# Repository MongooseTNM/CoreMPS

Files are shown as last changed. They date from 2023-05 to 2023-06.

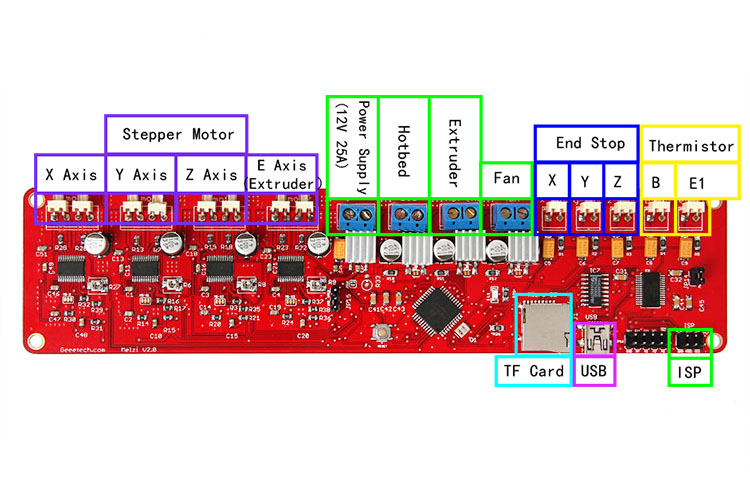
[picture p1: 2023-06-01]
Wiring Diagram.jpg

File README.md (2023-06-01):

# CoreMPS


The CoreMPS is a complete rebuild of the once-popular Monoprice Maker Select V2 3d printer. The CoreMPS replaces everything except the electronics, heater bed, and hot-end components. The frame was replaced with an aluminum extrusion cube design as opposed to the sheet metal the Monoprice Maker Select V2 came with. 

The CoreMPS also makes use of 3D-printed parts wherever possible in the spirit of RepRap. Reprap is a project started in 2010 that aims to allow printers to self-replicate, meaning that parts are designed and printed on the machine that the part was designed for. All the parts for the CoreMPS were designed with 3d printing in mind, there are no unprintable overhangs and the parts are strong enough to handle loads of high-speed printing. 

The CoreMPS uses CoreXY kinematics, meaning that 2 stationary motors move the gantry in both directions. When the motors rotate in the same direction the gantry will move left and right (X direction) and when the motors rotate in opposite directions then the gantry will move forward and backward (Y direction). If only one motor rotates the gantry will move at a 45-degree angle.

Building the CoreMPS requires pre-existing knowledge of building 3D printers and working with Raspberry Pis. The CoreMPS was designed from scratch over the course of a few weeks and built over the course of a week while parts arrived.

The CoreMPS is capable of printing at 300mm/s and 30k mm/s/s accelerations. Normal non-coreXY printers are usually capable of at most 100mm/s and 5k mm/s/s accelerations. This means that the CoreMPS can print objects up to 100% faster than normal non-coreXY printers.

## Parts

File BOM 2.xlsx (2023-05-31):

Item # | Thumbnail | Part Name | Part Number | Description | Make/Buy | Quantity | Vendor | Vendor Desc | Vendor P/N | Vendor URL | Vendor Price | Vendor Lot Size | Vendor Stock
 |  | MPS CoreXY | MPS CoreXY |  |  | 1
1 |  | HotBed | HotBed |  |  | 1
2 |  | 15mm Rev Extrusion 340mm Z | 15mm Rev Extrusion 340mm Z |  |  | 4
3 |  | 15mm Rev Extrusion 310mm X | 15mm Rev Extrusion 310mm X |  |  | 5
4 |  | 15mm Rev Extrusion 330mm Y | 15mm Rev Extrusion 330mm Y |  |  | 4
5 |  | MGN9H 300mm Y | MGN9H 300mm Y |  |  | 2
6 |  | Joint | Joint |  |  | 1
7 |  | MGN9H 250mm X | MGN9H 250mm X |  |  | 1
8 |  | Z Axis 8mm Linear Rod | Z Axis 8mm Linear Rod |  |  | 4
9 |  | Stepper Mount Z | Stepper Mount Z |  |  | 2
10 |  | Bottom Smooth Rod Mount Z | Bottom Smooth Rod Mount Z |  |  | 4
11 |  | Top Smooth Rod Mount Z | Top Smooth Rod Mount Z |  |  | 4
12 |  | Bed Mount | Bed Mount |  |  | 2
13 |  | Brass Nut | Brass Nut |  |  | 2
14 |  | LM8UU | LM8UU |  |  | 8
15 |  | i3_mk2 extruder | i3_mk2 extruder |  |  | 1
16 |  | Corner Brace | Corner Brace |  |  | 8
17 |  | F623ZZ Flange Bearing | F623ZZ Flange Bearing |  |  | 24
18 |  | Front Right Bearing Mount | Front Right Bearing Mount |  |  | 1
19 |  | Front Left Bearing Mount | Front Left Bearing Mount |  |  | 1
20 |  | Nema 17 34mm Lead Screw | Nema 17 34mm Lead Screw |  |  | 2
21 |  | Nema 17 48mm | Nema 17 48mm |  |  | 2
22 |  | GT2 20T5B_dz2020 | GT2 20T5B_dz2020 |  |  | 2
23 |  | Belts 4M needed | Belts 4M needed |  |  | 2
24 |  | Corner Gusset With Feet | Corner Gusset With Feet |  |  | 4
25 |  | Stepper Motor Mount Mirror | Stepper Motor Mount Mirror |  |  | 1
26 |  | Tall Bearing Spacer | Tall Bearing Spacer |  |  | 6
27 |  | Short Bearing Spacer | Short Bearing Spacer |  |  | 2
28 |  | Stepper Motor Bearing Brace | Stepper Motor Bearing Brace |  |  | 2
29 |  | Melzi Bracket | Melzi Bracket |  |  | 1
30 |  | Corner Gusset | Corner Gusset |  |  | 2
31 |  | Front Corner Gusset | Front Corner Gusset |  |  | 1
32 |  | melzi | melzi |  |  | 1
33 |  | Raspberry Pi Mount | Raspberry Pi Mount |  |  | 1
34 |  | Raspberry Pi 3B | Raspberry Pi 3B |  |  | 1
35 |  | Power Supply | Power Supply |  |  | 1
36 |  | Power Supply Mount | Power Supply Mount |  |  | 1
37 |  | Plug Mount | Plug Mount |  |  | 1
38 |  | Plug | Plug |  |  | 1
39 |  | Corner Bracket | Corner Bracket |  |  | 19

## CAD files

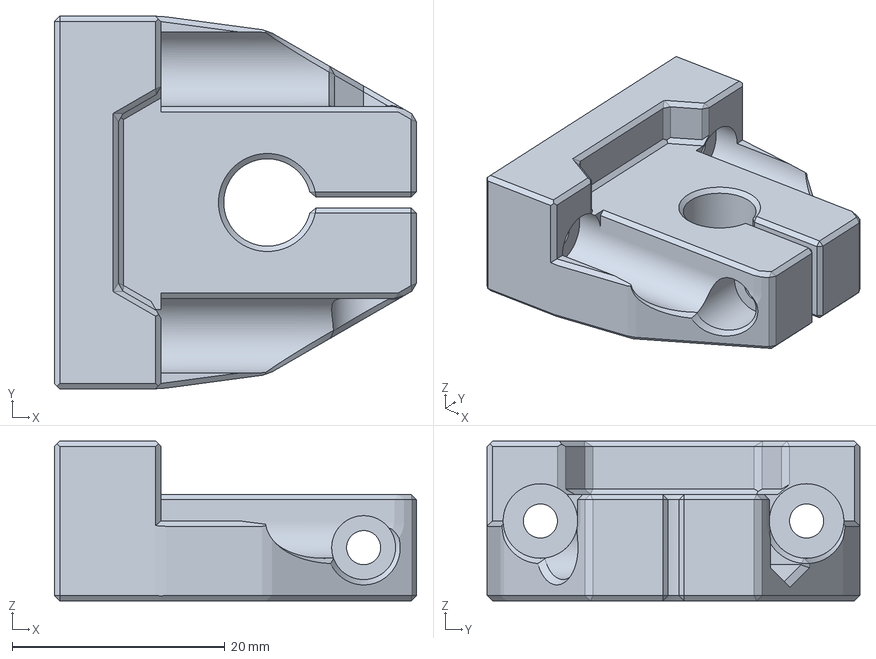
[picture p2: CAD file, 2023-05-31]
3D Printed Parts/4x Bottom Smooth Rod Mount Z v8.3mf
34.0 x 35.0 x 15.0 mm

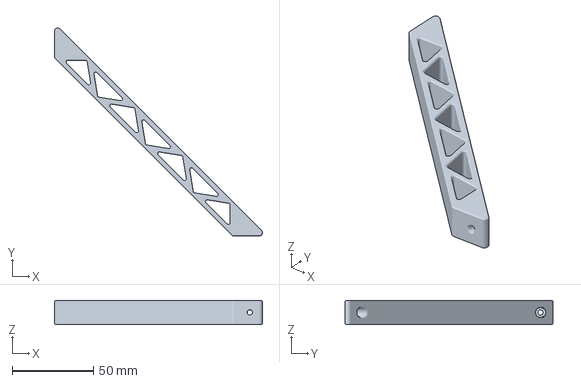
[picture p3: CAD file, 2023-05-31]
3D Printed Parts/8x Corner Brace v17.3mf
127.8 x 127.8 x 15.0 mm

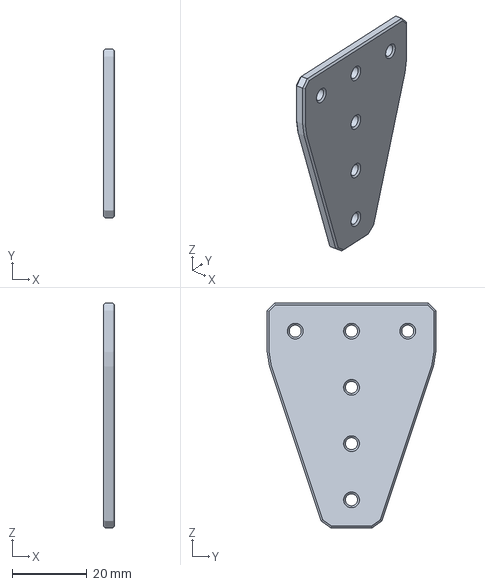
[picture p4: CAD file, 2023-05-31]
3D Printed Parts/3x 3 Way 180 Degree Corner Gusset v2.3mf
3.00 x 45.0 x 60.0 mm

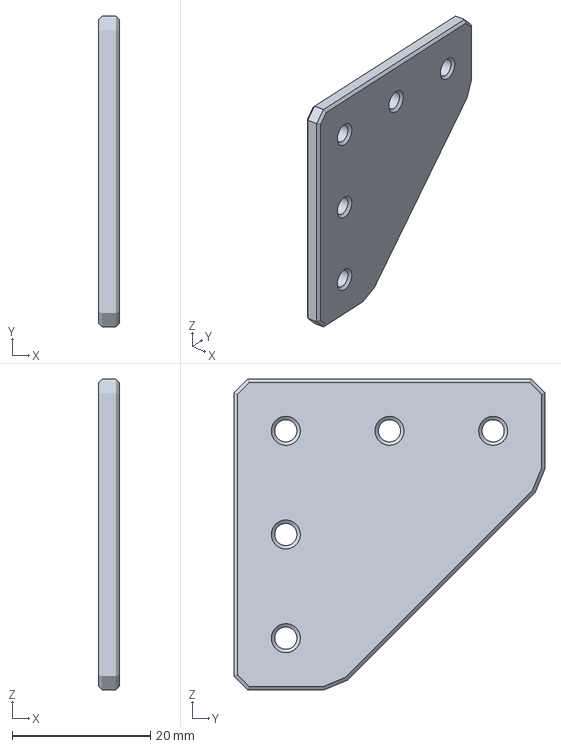
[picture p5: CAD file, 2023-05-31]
3D Printed Parts/2x 90 Degree Corner Gusset v2.3mf
3.00 x 45.0 x 45.0 mm

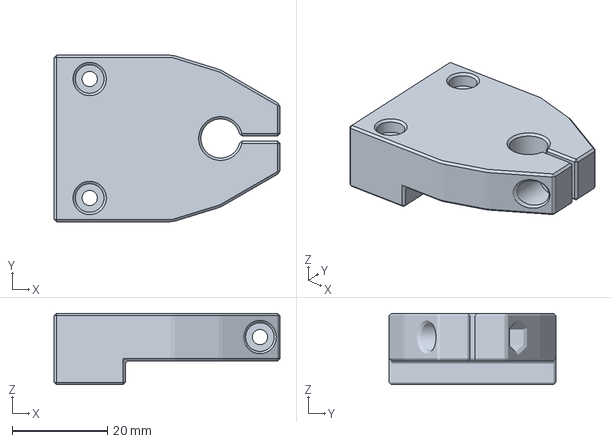
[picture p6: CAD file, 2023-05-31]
3D Printed Parts/4x Top Smooth Rod Mount Z v13.3mf
47.5 x 35.0 x 15.0 mm

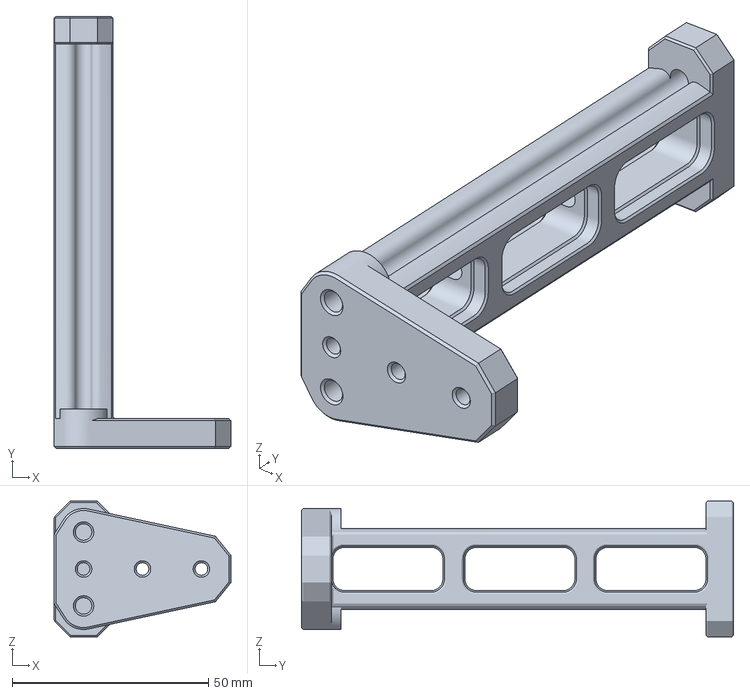
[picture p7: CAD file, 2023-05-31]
3D Printed Parts/1x Spool Holder.3mf
45.0 x 110.0 x 34.5 mm

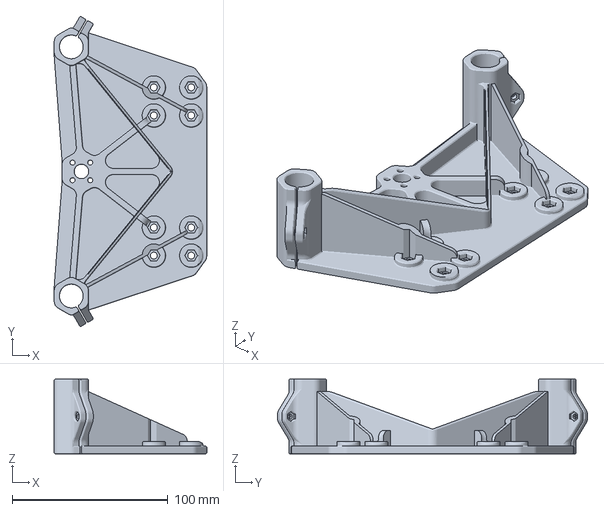
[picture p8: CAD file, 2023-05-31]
3D Printed Parts/2x Bed Mount v20.3mf
98.0 x 199.1 x 48.0 mm

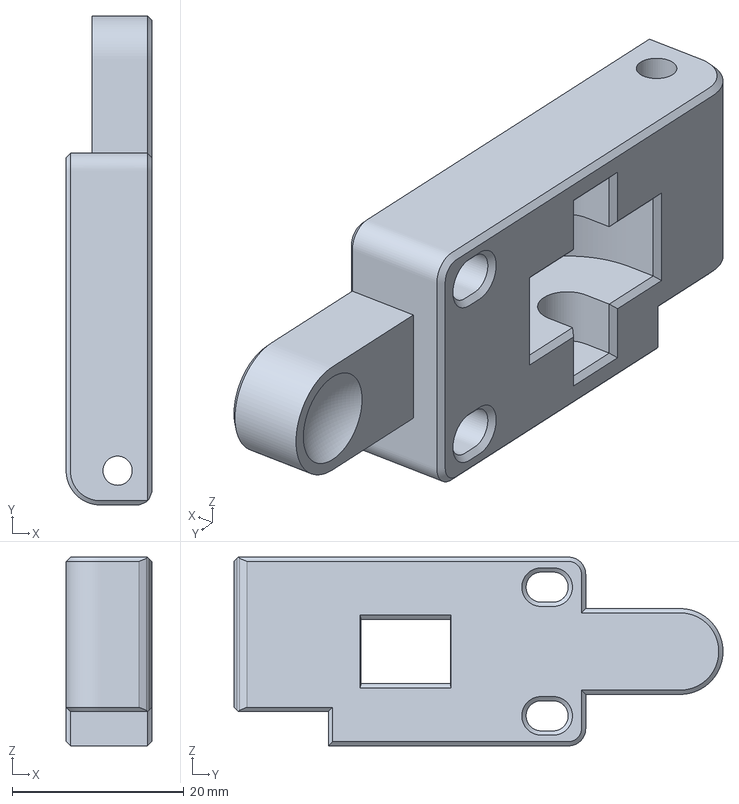
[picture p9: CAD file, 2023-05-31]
3D Printed Parts/1x Extruder Lever.3mf
10.0 x 57.0 x 22.0 mm

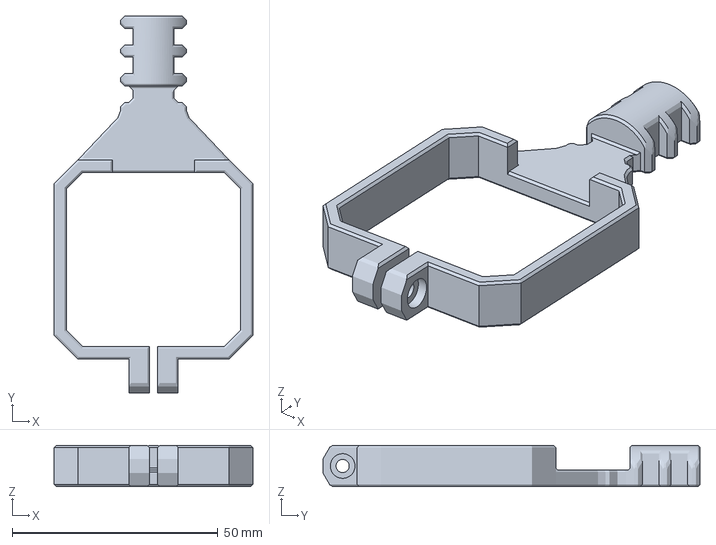
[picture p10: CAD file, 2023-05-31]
3D Printed Parts/1x Extruder Wire Management v5.3mf
48.3 x 91.6 x 10.0 mm

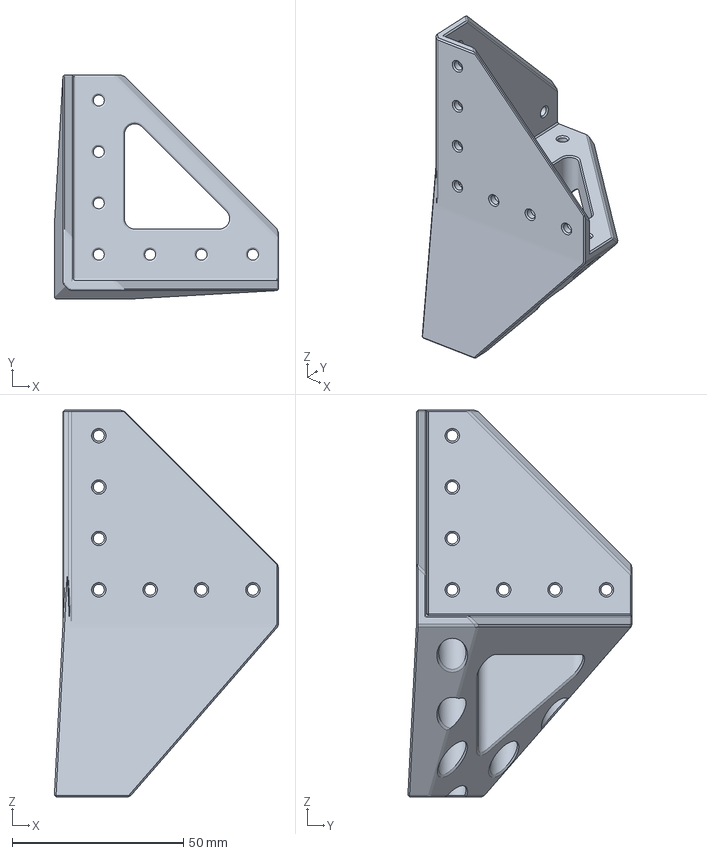
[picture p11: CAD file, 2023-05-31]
3D Printed Parts/4x Corner Gusset With Feet v13.3mf
65.5 x 65.5 x 113.0 mm

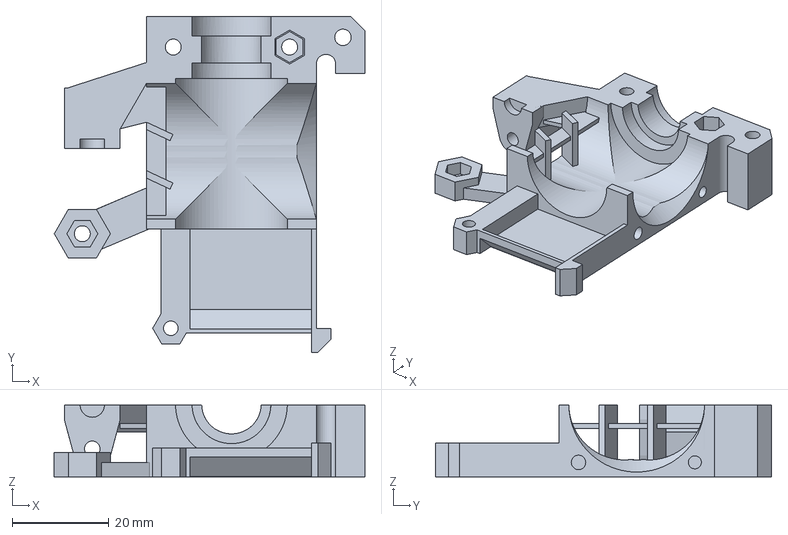
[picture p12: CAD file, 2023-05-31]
3D Printed Parts/1x Rail Extruder_cover_mod_Volcano v8.3mf
64.0 x 69.3 x 14.8 mm

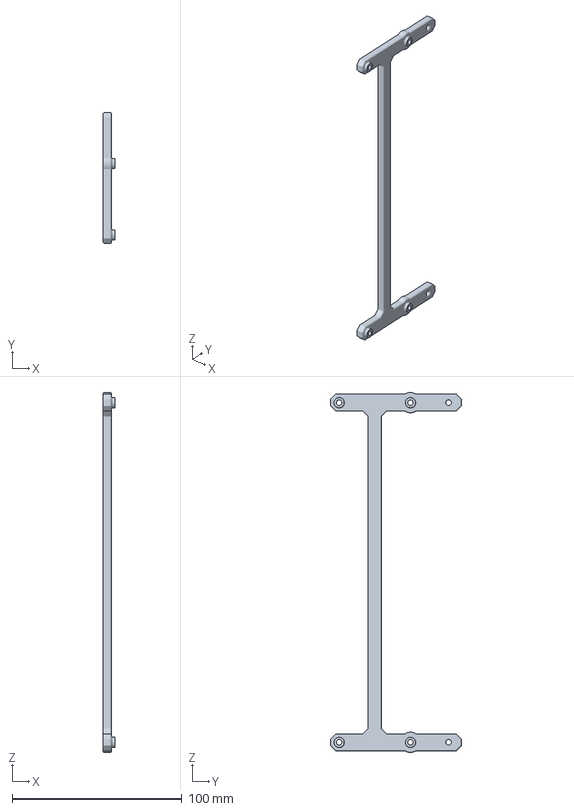
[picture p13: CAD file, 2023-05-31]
3D Printed Parts/1x Melzi Bracket v8.3mf
7.00 x 77.0 x 212.0 mm

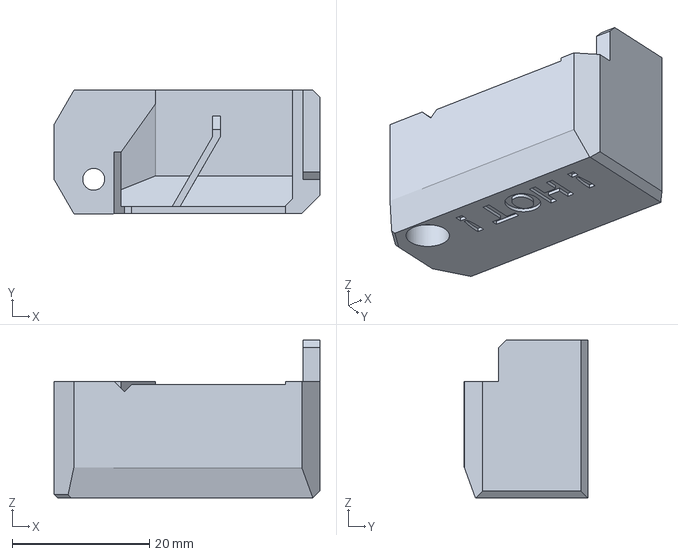
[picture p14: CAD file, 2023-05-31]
3D Printed Parts/1x Fan_Nozzle_E3D_Volcano_Prusa_I3_Mk2_V2 v20.3mf
38.8 x 18.0 x 23.0 mm

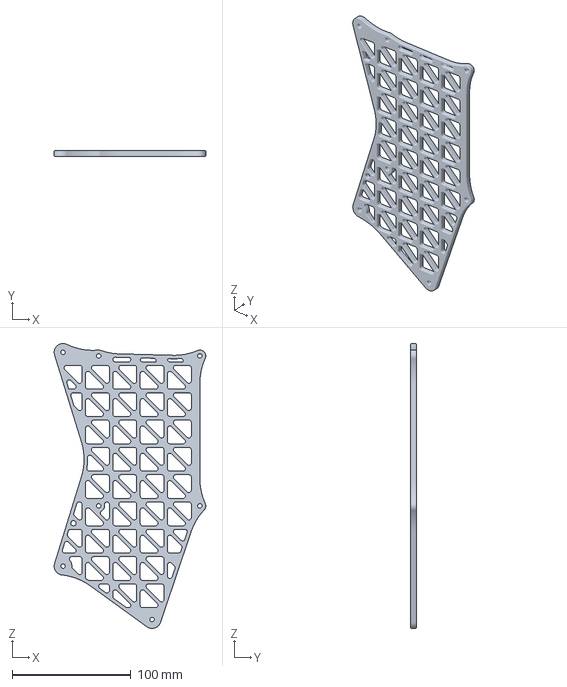
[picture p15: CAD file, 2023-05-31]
3D Printed Parts/1x Power Supply Mount v11.3mf
127.7 x 5.00 x 240.0 mm

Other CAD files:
3D Printed Parts/6x Tall Bearing Spacer v4.3mf
3D Printed Parts/1x Raspberry Pi Mount v6.3mf
3D Printed Parts/1x Wiring Mount Frame v4.3mf
3D Printed Parts/2x Stepper Motor Mount Tensioner v26.3mf
3D Printed Parts/19x Corner Bracket v3.3mf
3D Printed Parts/1x ADXL Mount Washer v2.3mf
3D Printed Parts/1x Bed Mosfet Mount v2.3mf
3D Printed Parts/1x Camera Mount v9.3mf
3D Printed Parts/1x Extruder Rail Mount.3mf
3D Printed Parts/1x Front Corner Gusset v16.3mf
3D Printed Parts/1x Front Left Bearing Mount v8.3mf
3D Printed Parts/1x Front Right Bearing Mount v8.3mf
3D Printed Parts/1x Joint v35.3mf
3D Printed Parts/1x Melzi Bracket v6.3mf
3D Printed Parts/1x Plug Mount v6.3mf
3D Printed Parts/1x Rail Extruder_body_mod_Volcano v13.3mf
3D Printed Parts/1x Stepper Motor Mount Mirror v20.3mf
3D Printed Parts/2x Bed Mount v16.3mf
3D Printed Parts/2x Corner Gusset v4.3mf
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
